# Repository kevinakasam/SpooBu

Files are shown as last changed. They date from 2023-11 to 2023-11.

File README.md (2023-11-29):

# SpooBu - A **Spoo**l **Bu**ffer aka Spool Rewinder

What if... we don't need a buffer but... rewind the filament back onto the spool...? This is SpooBu! A gravity-based filament spool rewinder. Imagine you're standing next to your printer and manually spinning the spool back when your MMU changes/unloads the filament. Since that would be very time-consuming, I invented SpooBu!

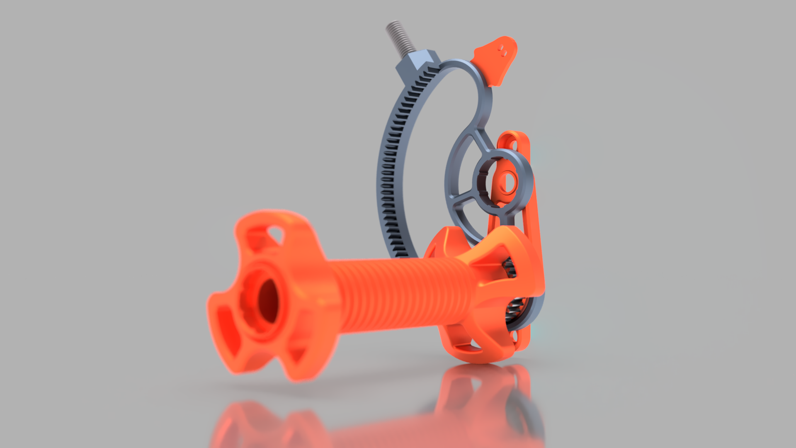
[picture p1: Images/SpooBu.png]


## How does it work?

It's a very simple mechanism: It's a spool holder with a counterweight that loads up as the spool spins, and then the counterweight spools the spool back up when the filament gets unloaded.

SpooBu is made out of three parts: a spool mount, a little gear on the spool mount, and a counterweight. When the printer feeds the filament, the spool starts to spin, and as the little gear is attached to the spool mount, it also spins. The little gear has contact with the counterweight, so when the spool spins, the little gear spins as well, which then spins the counterweight to move it upwards.
When the printer unloads the filament, the tension on the spool gets released, and the counterweight can move down again (thanks, gravity!). As it does that, it spins the little gear on the spool mount and therefore also the spool. Tadaa, your filament got rewound on the spool.

I did record a quick demonstration video of SpooBu (this is just a testing setup and very messy): https://youtu.be/ba3n2fLI1wE

Demo VID (https://youtu.be/ba3n2fLI1wE)

## What to print?

Print all the files from the `_Common` folder. If your measured filament length is already in the `STL` folder you're good for printing! If not you can super easily adapt the CAD for your filament length, even though if you never worked with CAD before! It's super simple and I showed every single step in the video linked further down. And before your world is falling apart, give me a ping on my or the Voron Discord and I will try my best to give you a set of files. Please make a Pull Reuest if you adapted the CAD for your length.

A little note about the filament length: I would substract ~20mm from the measured length so you dont risk to pull out the filament of the MMU (this never happened to me with my stock ERCF). To measure the length, just load the filament into the nozzle, add a little mark on the filament at the mmu, unload the filament and measure the length (a little bit like you tune e-steps).

The design is based on the [Universial Filament Spool Mount from PurchenZuPoden](https://www.printables.com/de/model/65651-universal-filament-spool-holder). Just download and print the mount from there (the nut and one of the mounts - the short mount works for regular sizes spools)

The `_Optional folder` contains some optional parts, you can use if you want. You can print some of the M8 screws, I use a printed M8x16mm screw for the counterweight axis which works very well. You can also print the nut-weight screw, but then you loose the weight of the screw. The ECAS holder is to properly route your PTFE Tubes - make sure that you have a proper PTFE routing! Everything should be nice and smooth and secure. The Files for the nut and screws are made with the [Nut Job Files](https://www.printables.com/de/model/94761-nut-job-nut-bolt-washer-and-threaded-rod-factory).

## How can I use it for my printer?

Simple answer: Parametric CAD design! Not much to say here, just measure the length of filament you have to buffer, paste that in the CAD file, print the files, and that's it :D. I made a little instruction video on how you can create your own set of files. Feel free to make a Pull Request with your files so others can use your files in case they have the same buffer length!

You need the [Helical Gear + Plugin](https://apps.autodesk.com/FUSION/de/Detail/Index?id=1259509007239787473&appLang=en&os=Mac) to adapt the CAD file!

I did record a short CAD tutorial how to adapt the Design: https://youtu.be/17P4wHjeBd8

CAD Tutorial (https://youtu.be/17P4wHjeBd8)

## BOM

Totally forgot the BOM^^ will add that later, but you need 3 608 bearings, three M8 screws with hex head (M8x16mm and a long M8 for the spool mount (I use a M8x140mm) and another screw for the couterweight) and quite some M8 nuts)

## Credits

Thanks to Pavel Hartmann for [his rewinder](https://youtu.be/otfgxMiwivw?si=FOWaNhXBAOYx1tBN) idea!

Thanks to all the people on my Discord for tinkering with me!

Thanks to [PurchenZuPoden](https://www.printables.com/de/model/65651-universal-filament-spool-holder) for the spool mount!

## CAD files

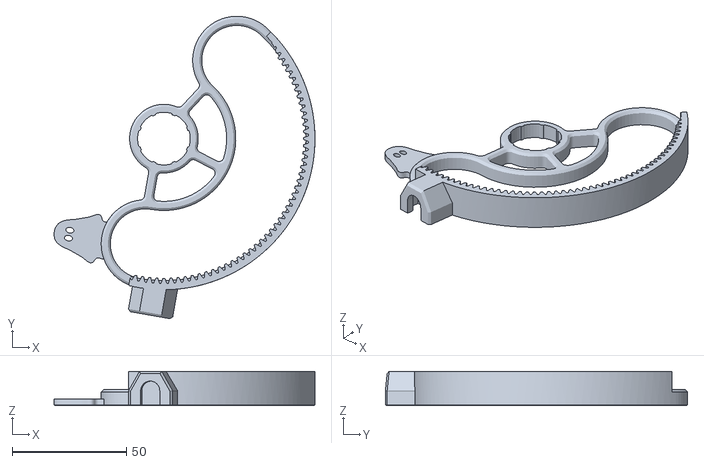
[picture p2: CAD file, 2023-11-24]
STL/1050mm/CounterWeight.stl
114.0 x 132.1 x 15.0

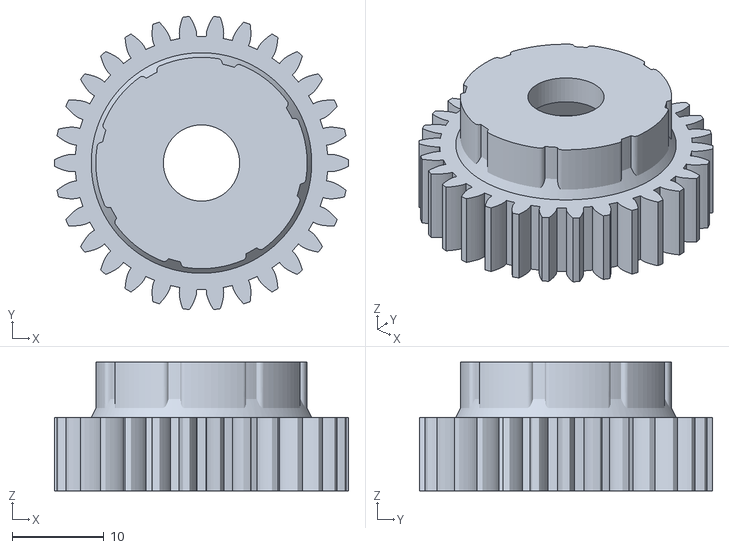
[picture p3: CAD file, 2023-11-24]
STL/_Common/Spool_Gear_x1.stl
32.0 x 31.9 x 14.0

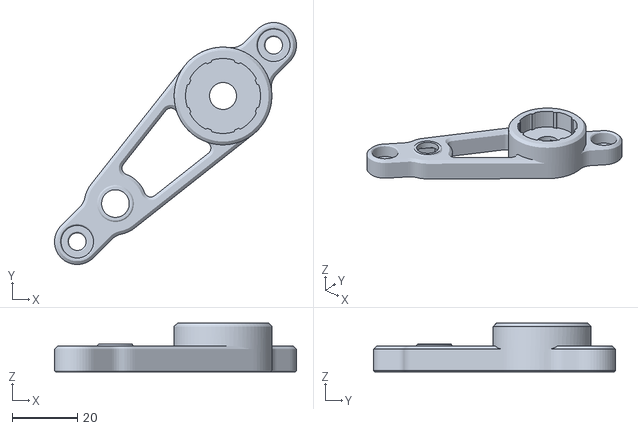
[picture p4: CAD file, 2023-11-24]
STL/1050mm/2020_Mount.stl
74.3 x 74.3 x 15.0

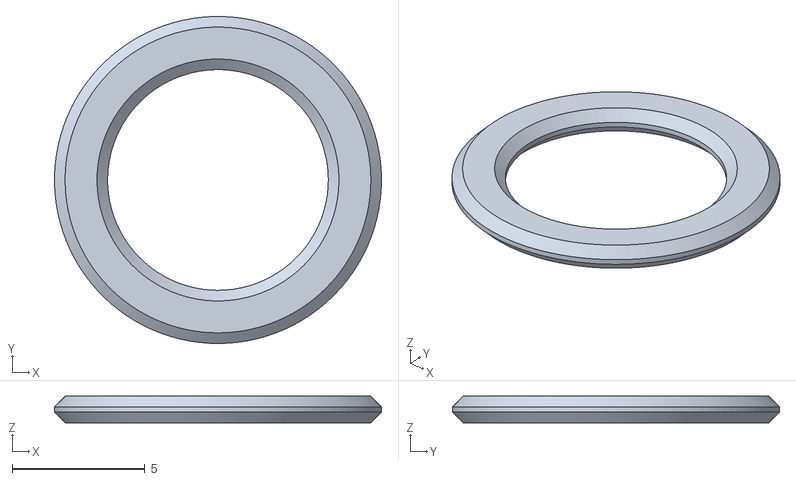
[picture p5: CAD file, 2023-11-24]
STL/_Common/Spacer_x1.stl
12.3 x 12.3 x 1.00

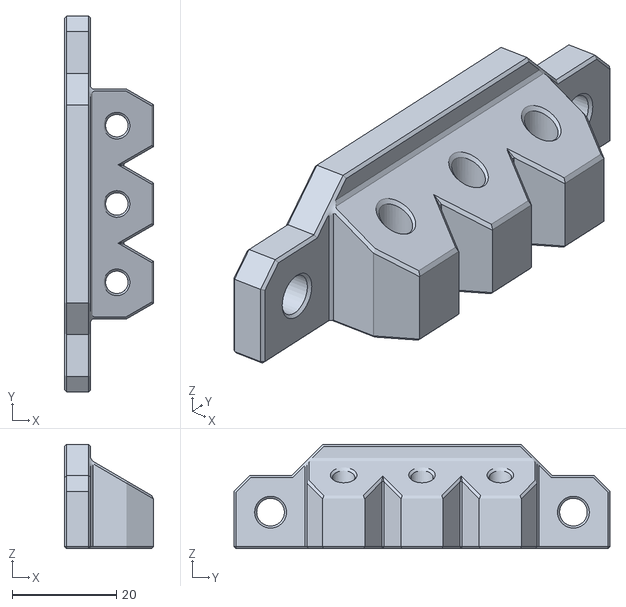
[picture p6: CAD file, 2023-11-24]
STL/_Optional/ECAS v2.stl
17.0 x 72.0 x 20.0

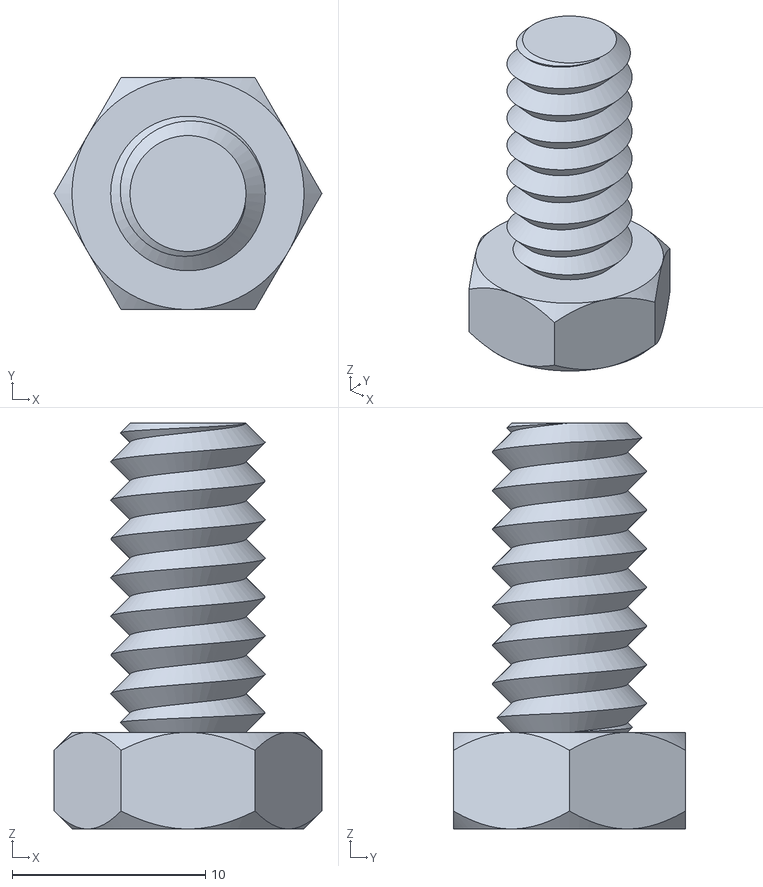
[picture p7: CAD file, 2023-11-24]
STL/_Optional/M8x16.stl
13.9 x 12.0 x 21.0

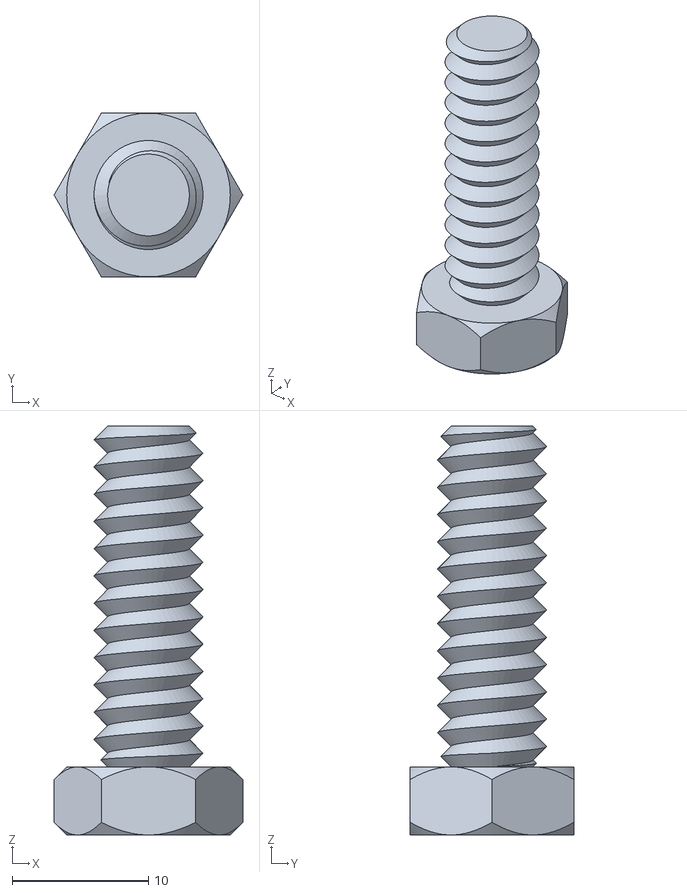
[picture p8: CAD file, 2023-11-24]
STL/_Optional/M8x25.stl
13.9 x 12.0 x 30.0

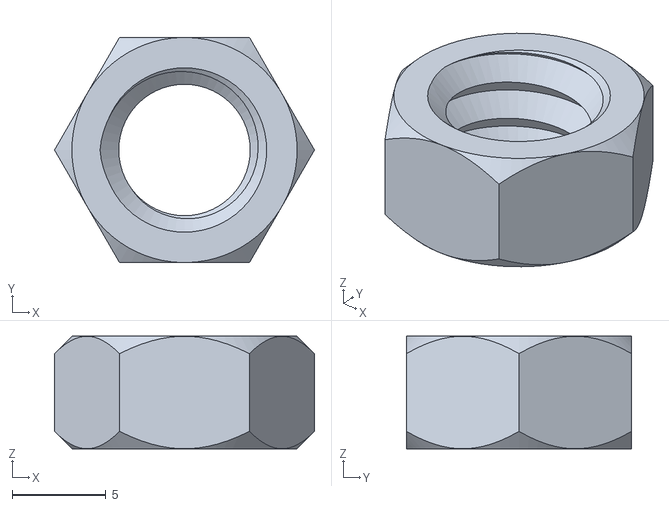
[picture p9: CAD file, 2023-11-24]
STL/_Optional/M8_Nut.stl
13.9 x 12.0 x 6.00

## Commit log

2023-11-24 Initial Release
    [2020_Mount.stl, CounterWeight.stl, ECAS v2.stl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]
2023-11-29 Better CAD
